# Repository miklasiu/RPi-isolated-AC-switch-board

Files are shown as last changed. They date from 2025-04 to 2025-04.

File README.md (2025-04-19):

# RPi isolated AC switch board
 24/110/230V AC triac switch board

The board is intended to be used as a garden watering control be me. Use for whatever you want yourselves. 
There is Python based software being developed thar runs on this hardware.
I used optotriac-trac because it is ~3 times less expenssive than cheapest relay and it should outlast any realy.
Triac introduces ~1.4V drop but it doesn't matter much for 24V and is negligible for 110V and up.

Borard can be made at home as a 1 side. All top-side connections can be made with wires. This is the way I did it.
For the Triac you can use BTA312. I was worried they won't trigger correctly with low voltage/current but they do without a problem.
I used BTA312-600 from WeEn but any low gate current, high voltage triac will likely work.

High side 10nF capacitor needs to be rated to peak-to-peak voltage (RMS_ACV*1.41). I used 500V ones.

I didn't use I2C eeprom at all. It was intended for RPi HAT configuration, but it works without it.

You can omit indicator LEDs and their resistors too.

Generally I put too much stuff here.

Oh there are 8 inputs for whatever use you wish inteded for dry contacts. NO VOLTAGE - just switches/contacts (water level, pressure)
And I2C connector with pinout for 0.91" OLED module. I don't use it too :).

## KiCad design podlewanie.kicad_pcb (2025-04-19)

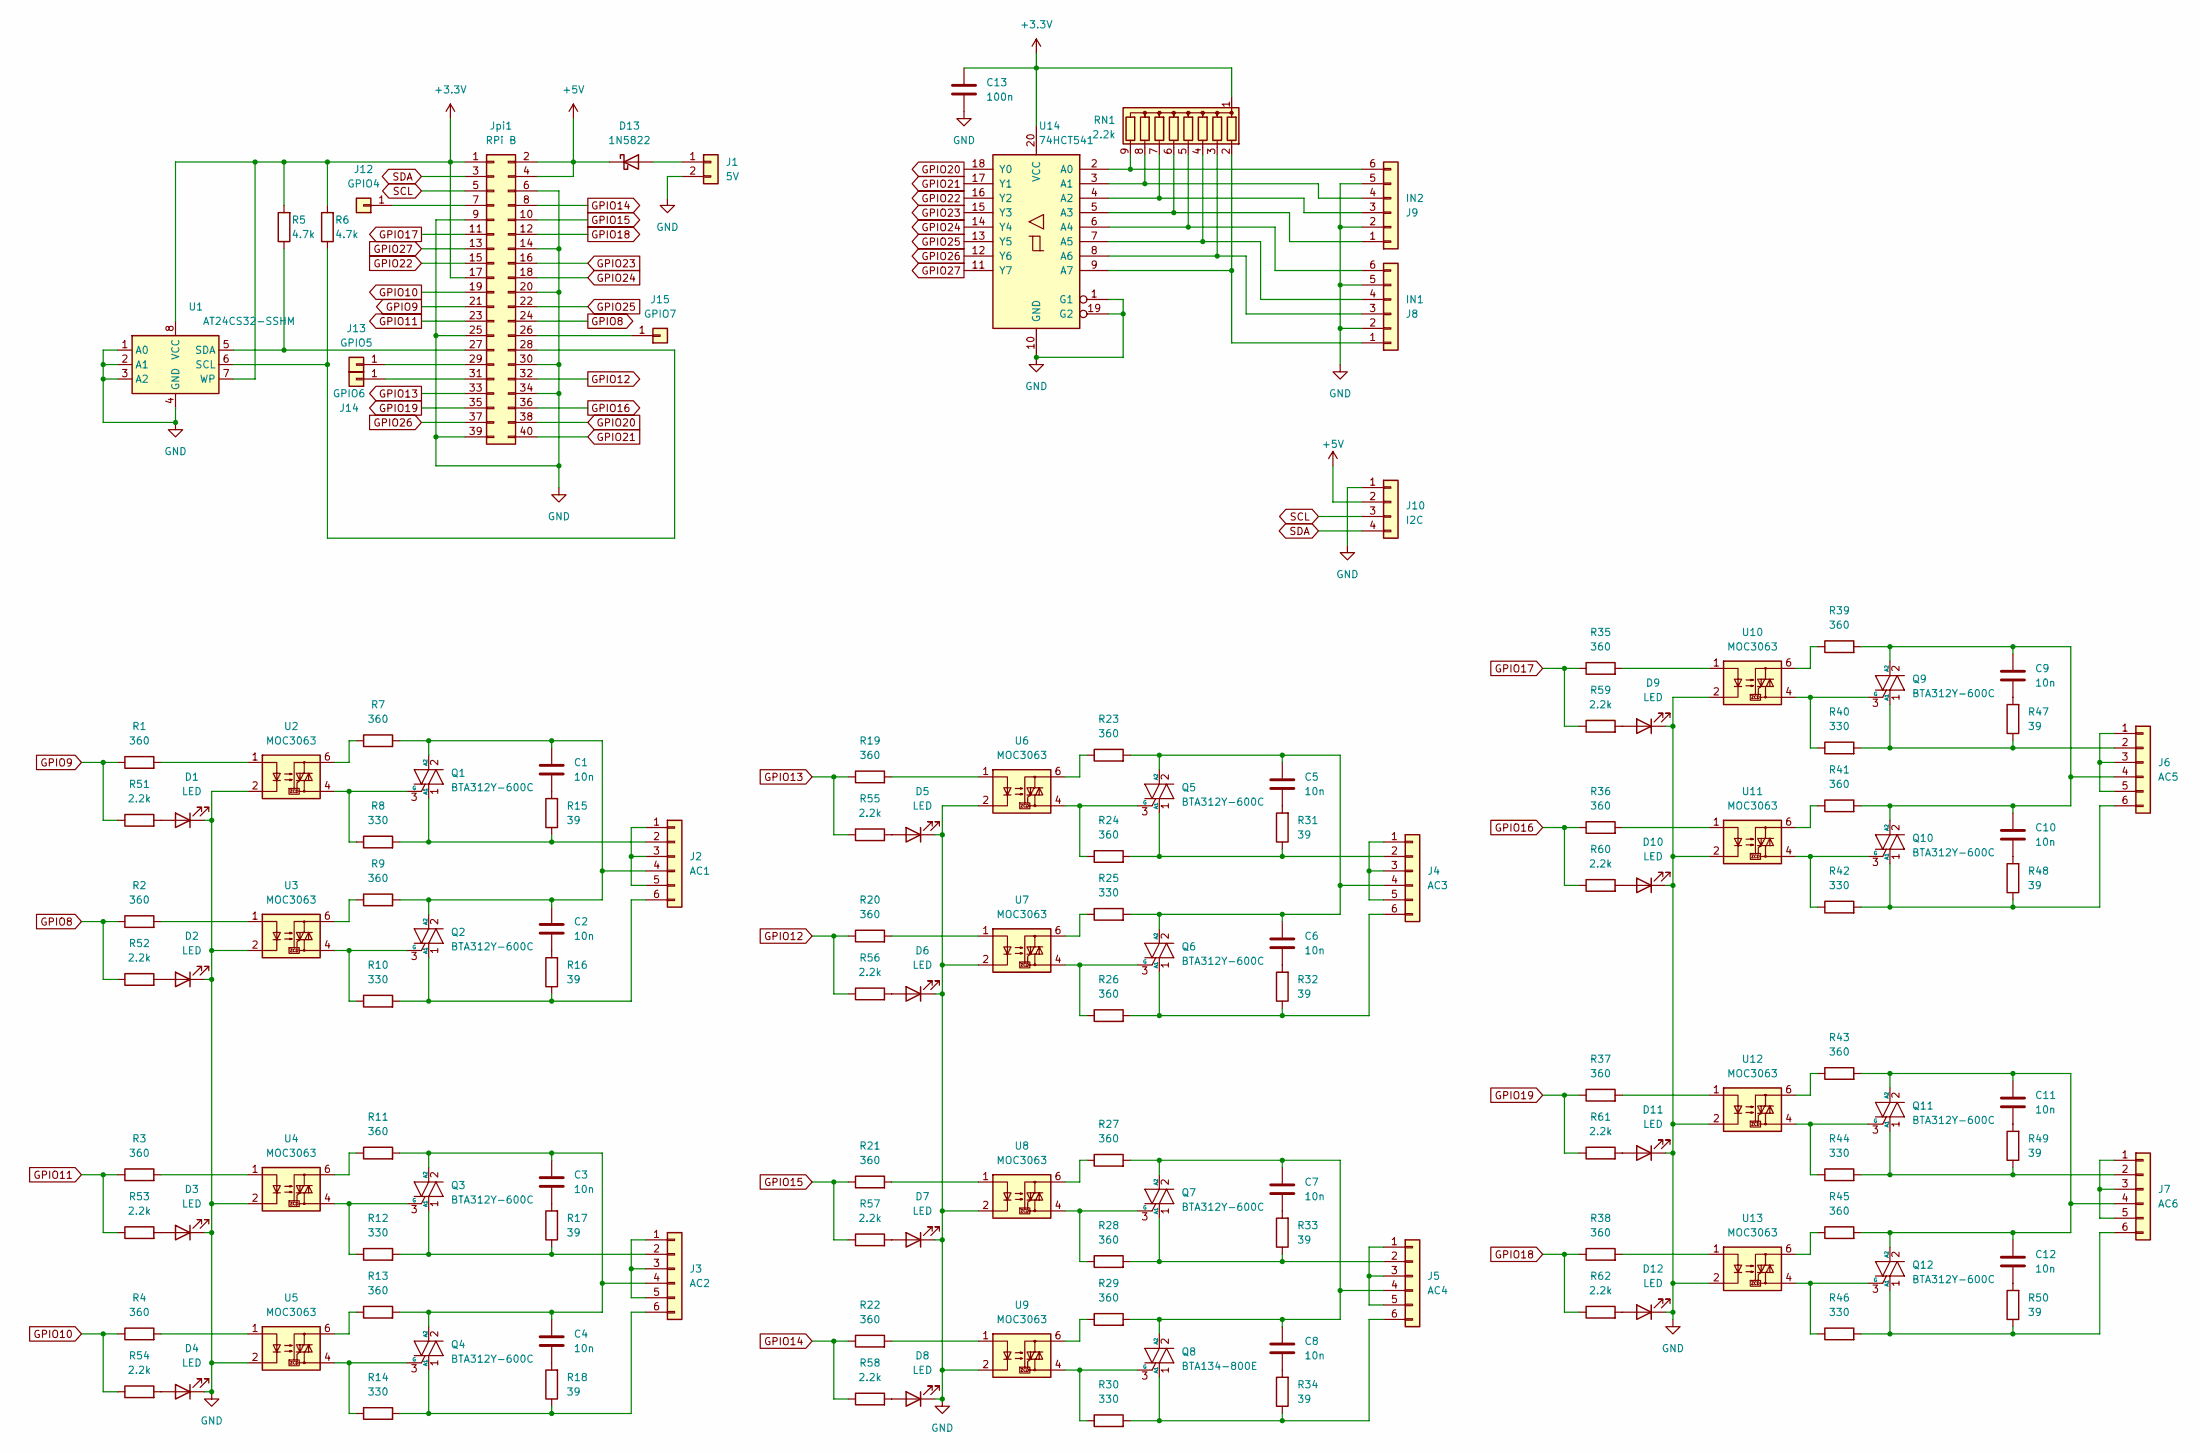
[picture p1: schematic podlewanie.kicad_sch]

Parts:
C1, C2, C3, C4, C5, C6, C7, C8, C9, C10, C11, C12: 10n; C_Disc_D9.0mm_W2.5mm_P5.00mm
C13: 100n; C_1206_3216Metric_Pad1.33x1.80mm_HandSolder
D1, D2, D3, D4, D5, D6, D7, D8, D9, D10, D11, D12: LED; LED_D3.0mm
D13: 1N5822; D_DO-201AD_P15.24mm_Horizontal
J1: 5V; Wago_734-162_1x02_P3.50mm_Horizontal
J2: AC1; Wago_734-166_1x06_P3.50mm_Horizontal
J3: AC2; Wago_734-166_1x06_P3.50mm_Horizontal
J4: AC3; Wago_734-166_1x06_P3.50mm_Horizontal
J5: AC4; Wago_734-166_1x06_P3.50mm_Horizontal
J6: AC5; Wago_734-166_1x06_P3.50mm_Horizontal
J7: AC6; Wago_734-166_1x06_P3.50mm_Horizontal
J8: IN1; Wago_734-166_1x06_P3.50mm_Horizontal
J9: IN2; Wago_734-166_1x06_P3.50mm_Horizontal
J10: I2C; PinSocket_1x04_P2.54mm_Vertical
J12: GPIO4; PinHeader_1x01_P2.54mm_Vertical
J13: GPIO5; PinHeader_1x01_P2.54mm_Vertical
J14: GPIO6; PinHeader_1x01_P2.54mm_Vertical
J15: GPIO7; PinHeader_1x01_P2.54mm_Vertical
Jpi1: RPi B; PinSocket_2x20_P2.54mm_Vertical
Q1, Q2, Q3, Q4, Q5, Q6, Q7, Q9, Q10, Q11, Q12: BTA312Y-600C; TO-220-3_Vertical
Q8: BTA134-800E; TO-220-3_Vertical
R1, R2, R3, R4, R7, R9, R11, R13, R19, R20, R21, R22, R23, R24, R26, R27, R28, R29, R35, R36, R37, R38, R39, R41, R43, R45: 360; R_1206_3216Metric_Pad1.30x1.75mm_HandSolder
R5, R6: 4.7k; R_1206_3216Metric_Pad1.30x1.75mm_HandSolder
R8, R10, R12, R14, R25, R30, R40, R42, R44, R46: 330; R_1206_3216Metric_Pad1.30x1.75mm_HandSolder
R15, R16, R17, R18, R31, R32, R33, R34, R47, R48, R49, R50: 39; R_1206_3216Metric_Pad1.30x1.75mm_HandSolder
R51, R52, R53, R54, R55, R56, R57, R58, R59, R60, R61, R62: 2.2k; R_1206_3216Metric_Pad1.30x1.75mm_HandSolder
RN1: 2.2k; R_Array_SIP9
U1: AT24CS32-SSHM; SOIC-8_3.9x4.9mm_P1.27mm
U2, U3, U4, U5, U6, U7, U8, U9, U10, U11, U12, U13: MOC3063; DIP-6_W10.16mm
U14: 74HCT541; SSOP-20_4.4x6.5mm_P0.65mm

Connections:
+3.3V: C13.1, Jpi1.1, Jpi1.17, R5.2, R6.2, RN1.1 (common), U1.7 (WP), U1.8 (VCC), U14.20 (VCC)
+5V: D13.1 (K), J10.2, Jpi1.2, Jpi1.4
GND: C13.2, D1.1 (K), D2.1 (K), D3.1 (K), D4.1 (K), D5.1 (K), D6.1 (K), D7.1 (K), D8.1 (K), D9.1 (K), D10.1 (K), D11.1 (K), D12.1 (K), J1.2, J8.2, J8.5, J9.2, J9.5, J10.1, Jpi1.6, Jpi1.9, Jpi1.14, Jpi1.20, Jpi1.25, Jpi1.30, Jpi1.34, Jpi1.39, U1.1 (A0), U1.2 (A1), U1.3 (A2), U1.4 (GND), U2.2, U3.2, U4.2, U5.2, U6.2, U7.2, U8.2, U9.2, U10.2, U11.2, U12.2, U13.2, U14.1 (G1), U14.10 (GND), U14.19 (G2)
GPIO8: Jpi1.24, R2.1, R52.1
GPIO9: Jpi1.21, R1.1, R51.1
GPIO10: Jpi1.19, R4.1, R54.1
GPIO11: Jpi1.23, R3.1, R53.1
GPIO12: Jpi1.32, R20.1, R56.1
GPIO13: Jpi1.33, R19.1, R55.1
GPIO14: Jpi1.8, R22.1, R58.1
GPIO15: Jpi1.10, R21.1, R57.1
GPIO16: Jpi1.36, R36.1, R60.1
GPIO17: Jpi1.11, R35.1, R59.1
GPIO18: Jpi1.12, R38.1, R62.1
GPIO19: Jpi1.35, R37.1, R61.1
GPIO20: Jpi1.38, U14.18 (Y0)
GPIO21: Jpi1.40, U14.17 (Y1)
GPIO22: Jpi1.15, U14.16 (Y2)
GPIO23: Jpi1.16, U14.15 (Y3)
GPIO24: Jpi1.18, U14.14 (Y4)
GPIO25: Jpi1.22, U14.13 (Y5)
GPIO26: Jpi1.37, U14.12 (Y6)
GPIO27: Jpi1.13, U14.11 (Y7)
unnamed: C1.2, R15.2
unnamed: C2.2, R16.2
unnamed: C3.2, R17.2
unnamed: C4.2, R18.2
unnamed: C5.2, R31.2
unnamed: C6.2, R32.2
unnamed: C7.2, R33.2
unnamed: C8.2, R34.2
unnamed: C9.2, R47.2
unnamed: C10.2, R48.2
unnamed: C11.2, R49.2
unnamed: C12.2, R50.2
unnamed: D1.2 (A), R51.2
unnamed: D2.2 (A), R52.2
unnamed: D3.2 (A), R53.2
unnamed: D4.2 (A), R54.2
unnamed: D5.2 (A), R55.2
unnamed: D6.2 (A), R56.2
unnamed: D7.2 (A), R57.2
unnamed: D8.2 (A), R58.2
unnamed: D9.2 (A), R59.2
unnamed: D10.2 (A), R60.2
unnamed: D11.2 (A), R61.2
unnamed: D12.2 (A), R62.2
unnamed: D13.2 (A), J1.1
unnamed: J2.1, J2.3, J2.5
unnamed: J2.2, Q1.1 (A1), R8.2, R15.1
unnamed: C1.1, C2.1, J2.4, Q1.2 (A2), Q2.2 (A2), R7.2, R9.2
unnamed: J2.6, Q2.1 (A1), R10.2, R16.1
unnamed: J3.1, J3.3, J3.5
unnamed: J3.2, Q3.1 (A1), R12.2, R17.1
unnamed: C3.1, C4.1, J3.4, Q3.2 (A2), Q4.2 (A2), R11.2, R13.2
unnamed: J3.6, Q4.1 (A1), R14.2, R18.1
unnamed: J4.1, J4.3, J4.5
unnamed: J4.2, Q5.1 (A1), R24.2, R31.1
unnamed: C5.1, C6.1, J4.4, Q5.2 (A2), Q6.2 (A2), R23.2, R25.2
unnamed: J4.6, Q6.1 (A1), R26.2, R32.1
unnamed: J5.1, J5.3, J5.5
unnamed: J5.2, Q7.1 (A1), R28.2, R33.1
unnamed: C7.1, C8.1, J5.4, Q7.2 (A2), Q8.2 (A2), R27.2, R29.2
unnamed: J5.6, Q8.1 (A1), R30.2, R34.1
unnamed: J6.1, J6.3, J6.5
unnamed: J6.2, Q9.1 (A1), R40.2, R47.1
unnamed: C9.1, C10.1, J6.4, Q9.2 (A2), Q10.2 (A2), R39.2, R41.2
unnamed: J6.6, Q10.1 (A1), R42.2, R48.1
unnamed: J7.1, J7.3, J7.5
unnamed: J7.2, Q11.1 (A1), R44.2, R49.1
unnamed: C11.1, C12.1, J7.4, Q11.2 (A2), Q12.2 (A2), R43.2, R45.2
unnamed: J7.6, Q12.1 (A1), R46.2, R50.1
unnamed: J8.1, RN1.2 (R1), U14.9 (A7)
unnamed: J8.3, RN1.3 (R2), U14.8 (A6)
unnamed: J8.4, RN1.4 (R3), U14.7 (A5)
unnamed: J8.6, RN1.5 (R4), U14.6 (A4)
unnamed: J9.1, RN1.6 (R5), U14.5 (A3)
unnamed: J9.3, RN1.7 (R6), U14.4 (A2)
unnamed: J9.4, RN1.8 (R7), U14.3 (A1)
unnamed: J9.6, RN1.9 (R8), U14.2 (A0)
unnamed: J12.1, Jpi1.7
unnamed: J13.1, Jpi1.29
unnamed: J14.1, Jpi1.31
unnamed: J15.1, Jpi1.26
unnamed: Jpi1.27, R5.1, U1.5 (SDA)
unnamed: Jpi1.28, R6.1, U1.6 (SCL)
unnamed: Q1.3 (G), R8.1, U2.4
unnamed: Q2.3 (G), R10.1, U3.4
unnamed: Q3.3 (G), R12.1, U4.4
unnamed: Q4.3 (G), R14.1, U5.4
unnamed: Q5.3 (G), R24.1, U6.4
unnamed: Q6.3 (G), R26.1, U7.4
unnamed: Q7.3 (G), R28.1, U8.4
unnamed: Q8.3 (G), R30.1, U9.4
unnamed: Q9.3 (G), R40.1, U10.4
unnamed: Q10.3 (G), R42.1, U11.4
unnamed: Q11.3 (G), R44.1, U12.4
unnamed: Q12.3 (G), R46.1, U13.4
unnamed: R1.2, U2.1
unnamed: R2.2, U3.1
unnamed: R3.2, U4.1
unnamed: R4.2, U5.1
unnamed: R7.1, U2.6
unnamed: R9.1, U3.6
unnamed: R11.1, U4.6
unnamed: R13.1, U5.6
unnamed: R19.2, U6.1
unnamed: R20.2, U7.1
unnamed: R21.2, U8.1
unnamed: R22.2, U9.1
unnamed: R23.1, U6.6
unnamed: R25.1, U7.6
unnamed: R27.1, U8.6
unnamed: R29.1, U9.6
unnamed: R35.2, U10.1
unnamed: R36.2, U11.1
unnamed: R37.2, U12.1
unnamed: R38.2, U13.1
unnamed: R39.1, U10.6
unnamed: R41.1, U11.6
unnamed: R43.1, U12.6
unnamed: R45.1, U13.6
SCL: J10.3, Jpi1.5
SDA: J10.4, Jpi1.3

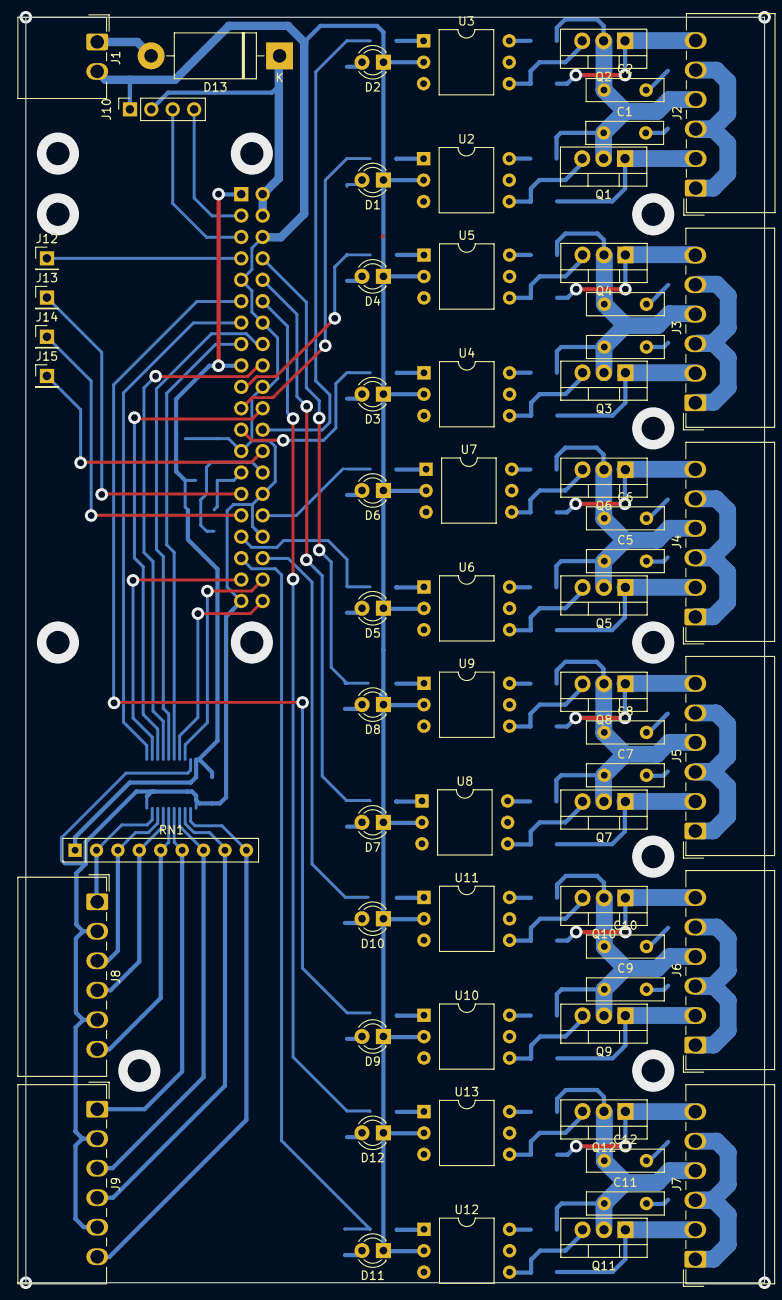
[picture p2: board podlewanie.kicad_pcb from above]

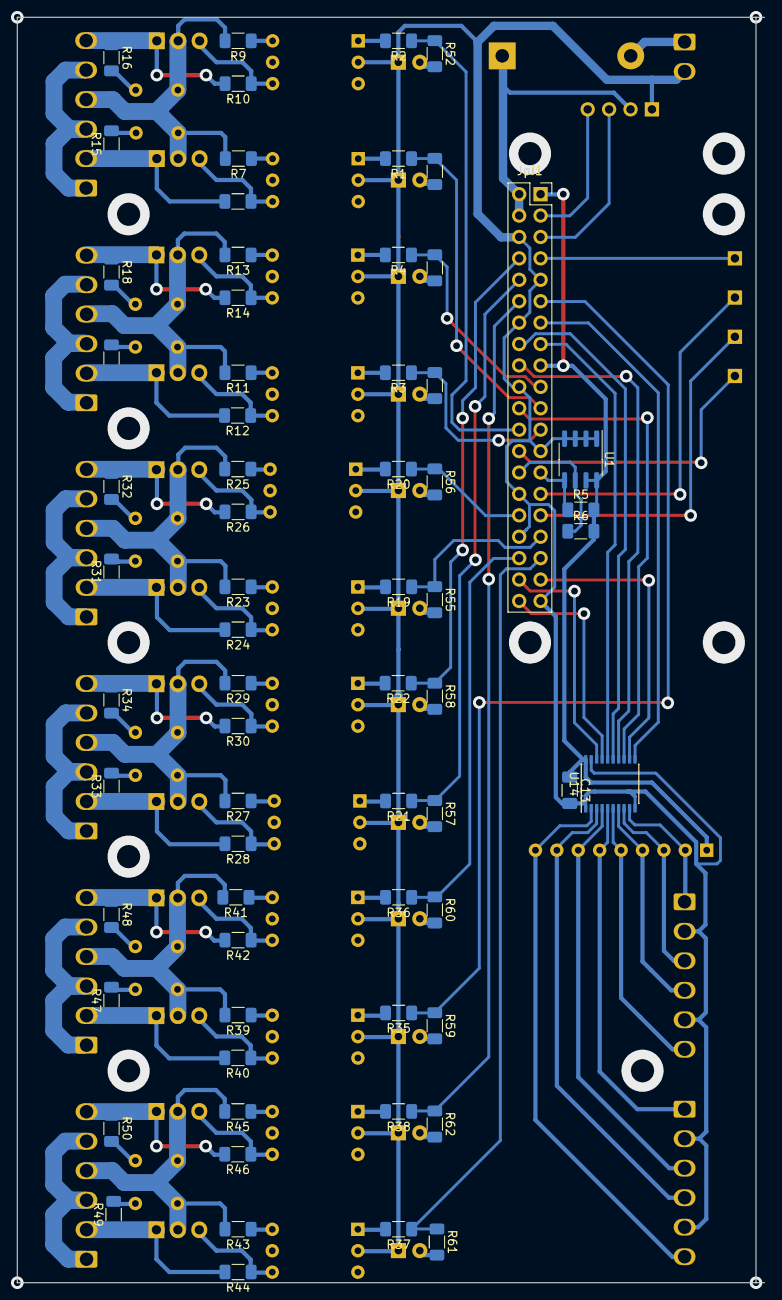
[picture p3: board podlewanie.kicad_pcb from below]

Board: 2 copper layers, 88.6 x 150.1 mm, 130 parts (66 on the bottom side), 124 nets.
